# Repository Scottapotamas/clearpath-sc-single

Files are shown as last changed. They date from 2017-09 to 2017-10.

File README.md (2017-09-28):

# clearpath-sc-single

A cut down board with similar electronics to the Clearpath SC4-Hub, but designed for single motor use.

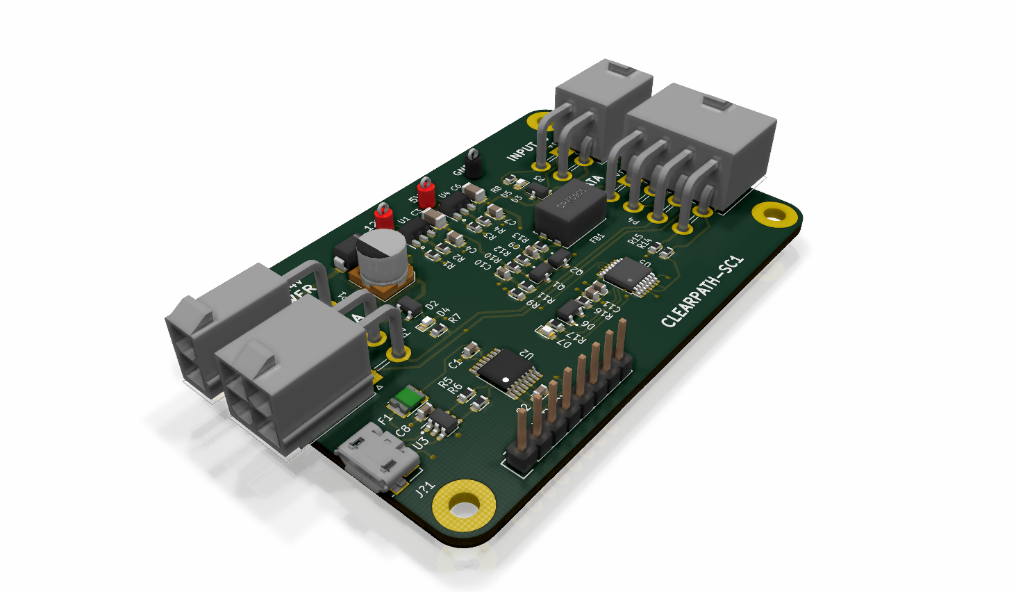
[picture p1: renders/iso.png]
Iso Render SC Single Render Iso View


## Overview

The Clearpath line of CNC servo motors from Teknic are great for robotics due to tight integration of controller and motor.

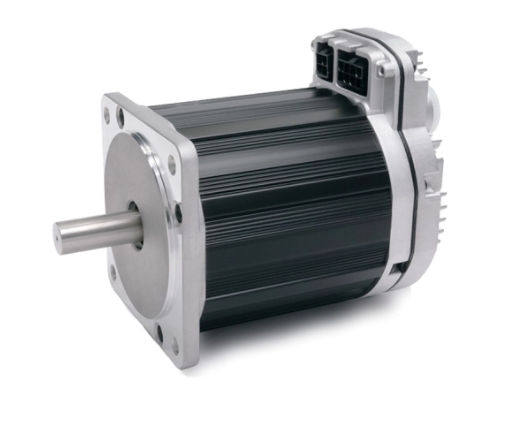
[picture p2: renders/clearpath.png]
Clearpath Motor

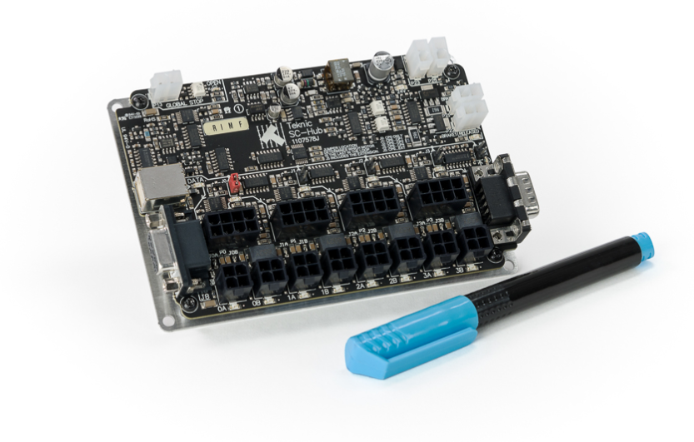
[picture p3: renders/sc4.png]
SC4 Hub Teknic's SC4 Hub


The SC series are software controllable, but rely on the use of a communications hub for level shifting and e-stop etc. This hub is designed to handle 4 motors and daisy chaining, and offers outputs to control brake solenoids and e-stop switches.

My application is space constrained and has no brake, so this single channel board offers the same main functionality (but we lose e-stop and brake outputs, and less defensive filtering on power input) in a reduced form factor. The serial input and USB functionality is maintained, and all OEM level hardening/filtering on communication lines on the SC4 is maintained. 

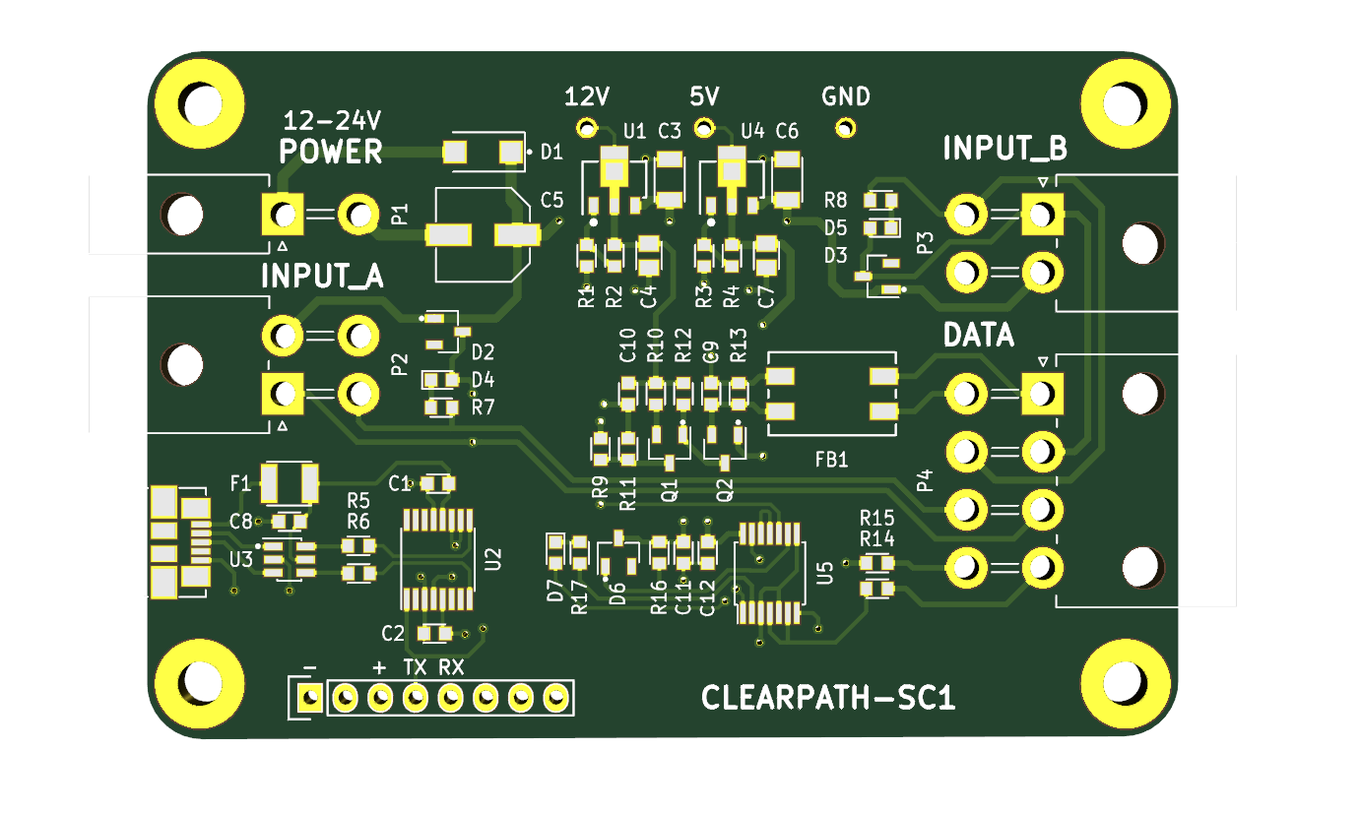
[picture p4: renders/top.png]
Top Render SC Single Render Top View


12-24V input power to provide signal level power. USB to serial is powered from the USB host. Header supports other TTL level serial devices if desired.

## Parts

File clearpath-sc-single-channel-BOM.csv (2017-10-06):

Title: | Single Channel Clearpath SC IO Board
Rev: | 1.0
Source: | /home/scott/projects/clearpath-sc-single/clearpath-sc-single-channel/clearpath-sc-single-channel.sch
Date: | Fri 06 Oct 2017 14:04:01 ACDT
Component Count: | 54
Ref | Qty | Value | Description | Manf | Manf# | Installed | Footprint
C1, C2, C8, C10, C11, C12 | 6 | 100NF_X7R_1608M | CAP, MLCC, X7R, 100NF, 50V, 0603 | KEMET | C0603C104K5RACAUTO |  | CAPC1608X90N
C3, C6 | 2 | 1UF_X7R_3216M | CAP, MLCC, X7R, 1UF, 100V, 1206, 3216M | TDK | C3216X7R2A105K160AA |  | CAPC3216X135N
C4, C7 | 2 | 1UF_X7R_2012M | CAP, MLCC, X7R, 1UF, 16V, 0805, 2012M | MURATA | GRM21BR71C105KA01L |  | CAPC2012X110N
C5 | 1 | 100UF_ELEC_35V_660X580M | CAP, ALU ELEC, 100UF, 35V, SMD | PANASONIC | EEEFT1V101AP |  | CAPAE660X580DD180L260N
C9 | 1 | 33NF_X7R_1608M | CAP, MLCC, X7R, 33NF, 50V, 0603 | KEMET | C0603C333K5RACAUTO |  | CAPC1608X90N
D1 | 1 | 1000V_1A_SODFL5125 | DIODE, 1000V, 1A, DO-214AC | MULTICOMP | S1M |  | SODFL5125X250N
D2, D3, D6 | 3 | BAS21_SOT23 | DIODE, 250V, 1.25Vfd, 2A surge, 50ns, SOT23 | ON SEMICONDUCTOR | BAS21 |  | SOT95P240X110-3L16N
D4, D5, D7 | 3 | LED_GREEN_1608M | DIALIGHT ChipLED Green, 0603, 1608M | DIALIGHT | 5988070107F |  | LEDC1608X80L40N
F1 | 1 | 500mA_1210L_PTC | FUSE, RESETTABLE, PTC, 13.2VDC, 500mA, SMD, 1210L050 | LittelFuse | 1210L050YR |  | FUSC3225X85L50N
FB1 | 1 | CHOKE_6500uH_300mA_0.3-2MHz | LINE FILTER, 6500uH, 80V, 300mA, 0.3-2Mhz, SMD | BOURNS | SRF0905-652Y |  | SRF0905
J?1 | 1 | USB_MICRO_B_SMD_2 | MICRO USB B RIGHT ANGLE FEMALE MOLEX | Molex | 47346-0001 |  | MOLEX_47346-0001
P1 | 1 | MOLEX_MICROFIT_JR_RH_2x1_WAY | CONNECTOR, SOCKET, 2POS, 1ROW, MICRO-FIT JR, 5569 series, 4.2MM pitch, PTH | MOLEX | 50-36-2457 |  | Molex_MiniFit-JR-5569-02A2_2x01x4.20mm_Angled
P2, P3 | 2 | MOLEX_MICROFIT_JR_RH_2x2_WAY | CONNECTOR, SOCKET, 4POS, 2ROW, MICRO-FIT JR, 5569 series, 4.2MM pitch, PTH | MOLEX | 26-01-3115 |  | Molex_MiniFit-JR-5569-04A2_2x02x4.20mm_Angled
P4 | 1 | MOLEX_MICROFIT_JR_RH_2x4_WAY | CONNECTOR, SOCKET, 8POS, 4ROW, MICRO-FIT JR, 5569 series, 4.2MM pitch, PTH | MOLEX | 172448-0008 |  | Molex_MiniFit-JR-5569-08A2_2x04x4.20mm_Angled
P5 | 1 | CONN_01X08 | Pin Header, 2.54mm, Vertical, PTH, 8 Way, 1 Row, 01x08 | WURTH | 61300811121 |  | 61300811121
Q1 | 1 | MMBT5401 | Transistor, PNP, -150V, 300MHz, 600mA, 250mW, SOT23 | ON SEMI | MMBT5401 |  | SOT95P240X110-3L16N
Q2 | 1 | MMBTA06 | Transistor, NPN, 80V, 100MHz, 500mA, 350mW, SOT-23 | ON SEMI | MMBTA06 |  | SOT95P240X110-3L16N
R1 | 1 | 2K2_1608M | RESISTOR, THICK FILM, 2.2K, 100mW, 1%, 0603, 1608M | VISHAY | CRCW06032K20FKEA |  | RESC1608X50N
R10 | 1 | 768R_1608M | RESISTOR, THICK FILM, 768R, 100mW, 1%, 0603, 1608M | PANASONIC | ERJ3EKF7680V |  | RESC1608X50N
R11 | 1 | 4K7_1608M | RESISTOR, THICK FILM, 100K, 125mW, 1%, 0603, 1608M | MULTICOMP | MC0063W060354K7 |  | RESC1608X50N
R12 | 1 | 93K1_1608M | RESISTOR, THICK FILM, 93.1K, 100mW, 1%, 0603, 1608M | VISHAY | CRCW060393K1FKEA |  | RESC1608X50N
R13 | 1 | 560R_1608M | RESISTOR, THICK FILM, 560R, 125mW, 1%, 0603, 1608M | MULTICOMP | MC0201L6F5600SE |  | RESC1608X50N
R14, R15 | 2 | 62R_1608M | RESISTOR, THICK FILM, 62R, 63mW, 0603, 1608M | MULTICOMP | MC00625W0402162R |  | RESC1608X50N
R16 | 1 | 470K_1608M | RESISTOR, THICK FILM, 470K, 100mW, 1%, 0603, 1608M | PANASONIC | ERJ3EKF4703V |  | RESC1608X50N
R17 | 1 | 390R_1608M | RESISTOR, THICK FILM, 390R, 63mW, 1%, 0603, 1608M | MULTICOMP | MC0063W06031390R |  | RESC1608X50N
R2, R4 | 2 | 240R_1608M | RESISTOR, THICK FILM, 240R, 100mW, 1%, 0603, 1608M | VISHAY DRALORIC | CRCW0603240RFKEA |  | RESC1608X50N
R3 | 1 | 750R_1608M | RESISTOR, THICK FILM, 750R, 100mW, 0603, 1608M | PANASONIC | ERJ3GEYJ751V |  | RESC1608X50N
R5, R6 | 2 | 22R_1608M | RESISTOR, THICK FILM, 22R, 125mW, 1%, 0603, 1608M | MULTICOMP | MC0063W060314R22 |  | RESC1608X50N
R7, R8 | 2 | 2K40_1608M | RESISTOR, THICK FILM, 2K4, 63mW, 1%, 0603, 1608M | MULTICOMP | MC0063W060312K4 |  | RESC1608X50N
R9 | 1 | 1K00_1608M | RESISTOR, THICK FILM, 1K, 125mW, 1%, 0603, 1608M | MULTICOMP | MCHP03W8F1001T5E |  | RESC1608X50N
TEST1, TEST2 | 2 | CLIP_HOOK_RED | PCB Probe Hook, RED, Through Hole | KEYSTONE | 5000 |  | KEYSTONE_5000
TEST3 | 1 | CLIP_HOOK_BLACK | PCB Probe Hook, BLACK, Through Hole | KEYSTONE | 5001 |  | KEYSTONE_5001
U1, U4 | 2 | LM317LCPK | ADJUSTABLE LINEAR REGULATOR, 1.2V TO 32V, SOT89-3 | TEXAS INSTRUMENTS | LM317LCPK |  | SOT89N
U2 | 1 | FT230XS-R | USB-UART/FIFO, USB2.0, FT230, SMD, TSSOP-16 | FTDI | FT230XS-R |  | SOP16P65_500X640X120L62X24N
U3 | 1 | USBLC6 | USBLC6-2 Low capacitance ESD Protection IC | ST | USBLC6-2SC6 |  | SOT95P280X145-6L50N
U5 | 1 | SN74HC14PWR | No description | TI | SN74HC14PWR |  | SOP14P65_500X640X120L62X24N
Tool: | Eeschema no-vcs-found
Script: | /home/scott/projects/ECAD/kicad-scripts/BOM/bom/BOM-GroupedByValue.py

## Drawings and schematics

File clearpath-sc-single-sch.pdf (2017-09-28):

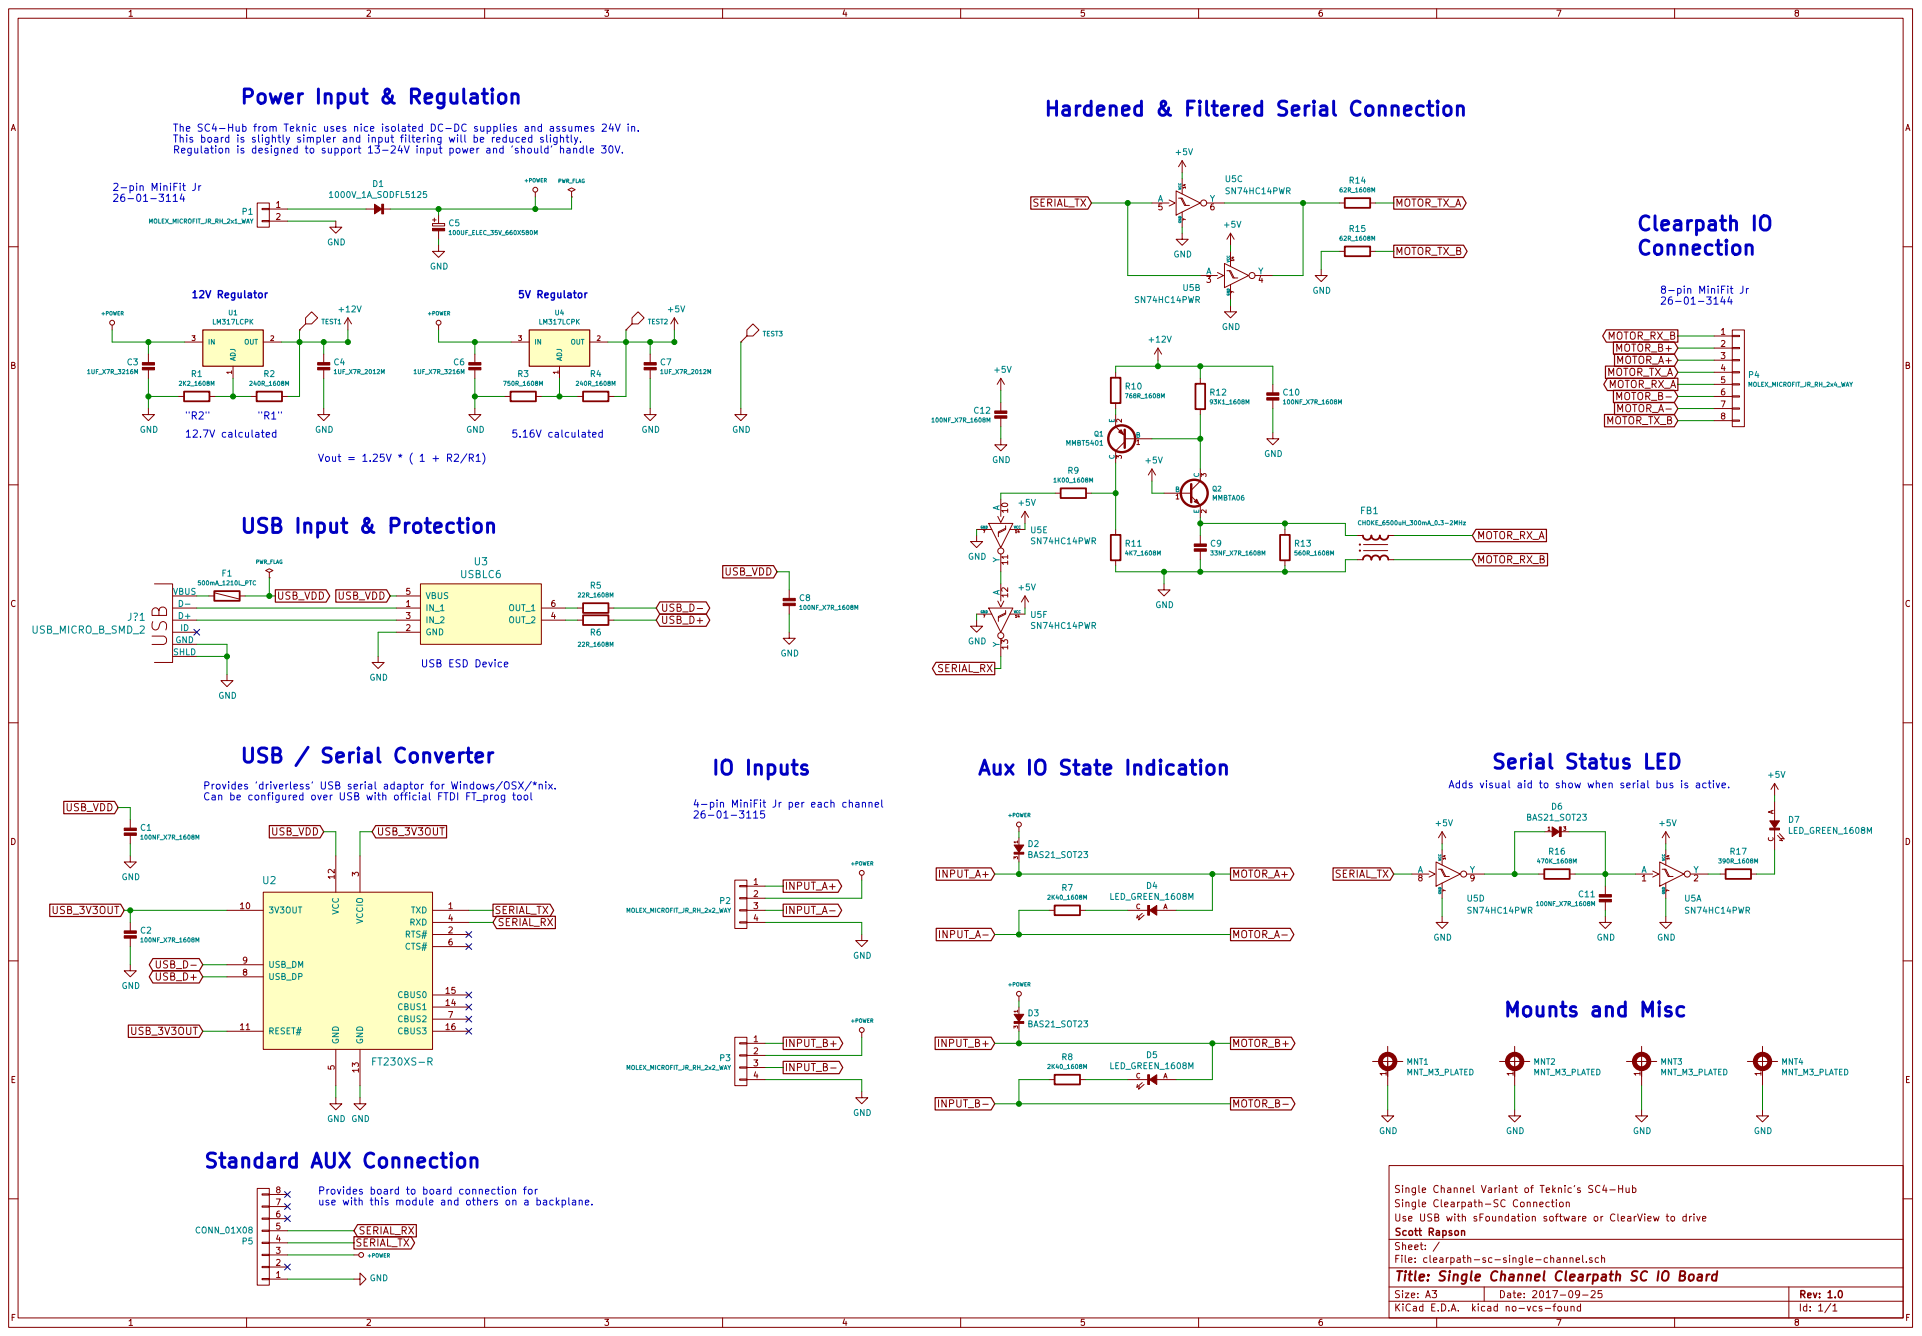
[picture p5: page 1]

4-pin MiniFit Jr per each channel 26-01-3115 Power Input & Regulation

Hardened & Filtered Serial Connection
8-pin MiniFit Jr 26-01-3144 Mounts and Misc

The SC4-Hub from Teknic uses nice isolated DC-DC supplies and assumes 24V in.
This board is slightly simpler and input filtering will be reduced slightly.

Single Channel Variant of Teknic's SC4-Hub USB VBUS D- D+

Aux IO State Indication

1 3 D3BAS21_SOT23 +POWER GND Adds visual aid to show when serial bus is active. USB_D-

Provides 'driverless' USB serial adaptor for Windows/OSX/*nix.
Can be configured over USB with official FTDI FT_prog tool

1 MNT1 MNT_M3_PLATED 1 MNT2 MNT_M3_PLATED 1 MNT3 MNT_M3_PLATED 1 MNT4 MNT_M3_PLATED GND GND GND GND

Provides board to board connection for use with this module and others on a backplane.

File: clearpath-sc-single-channel.sch Sheet: / Scott Rapson Use USB with sFoundation software or ClearView to drive Single Clearpath-SC Connection

Id: 1/1 Title: Single Channel Clearpath SC IO Board

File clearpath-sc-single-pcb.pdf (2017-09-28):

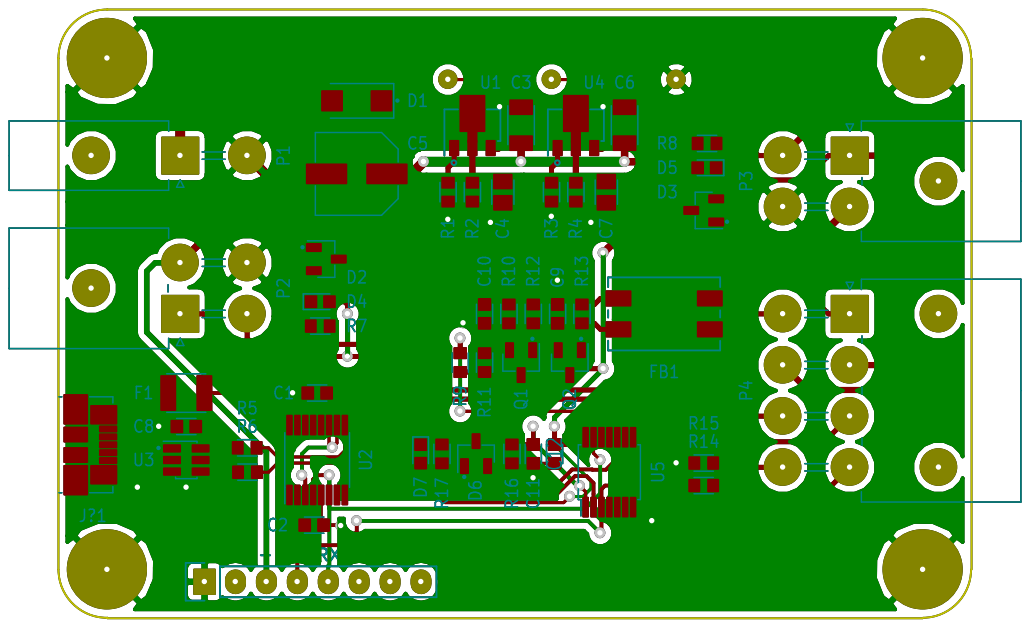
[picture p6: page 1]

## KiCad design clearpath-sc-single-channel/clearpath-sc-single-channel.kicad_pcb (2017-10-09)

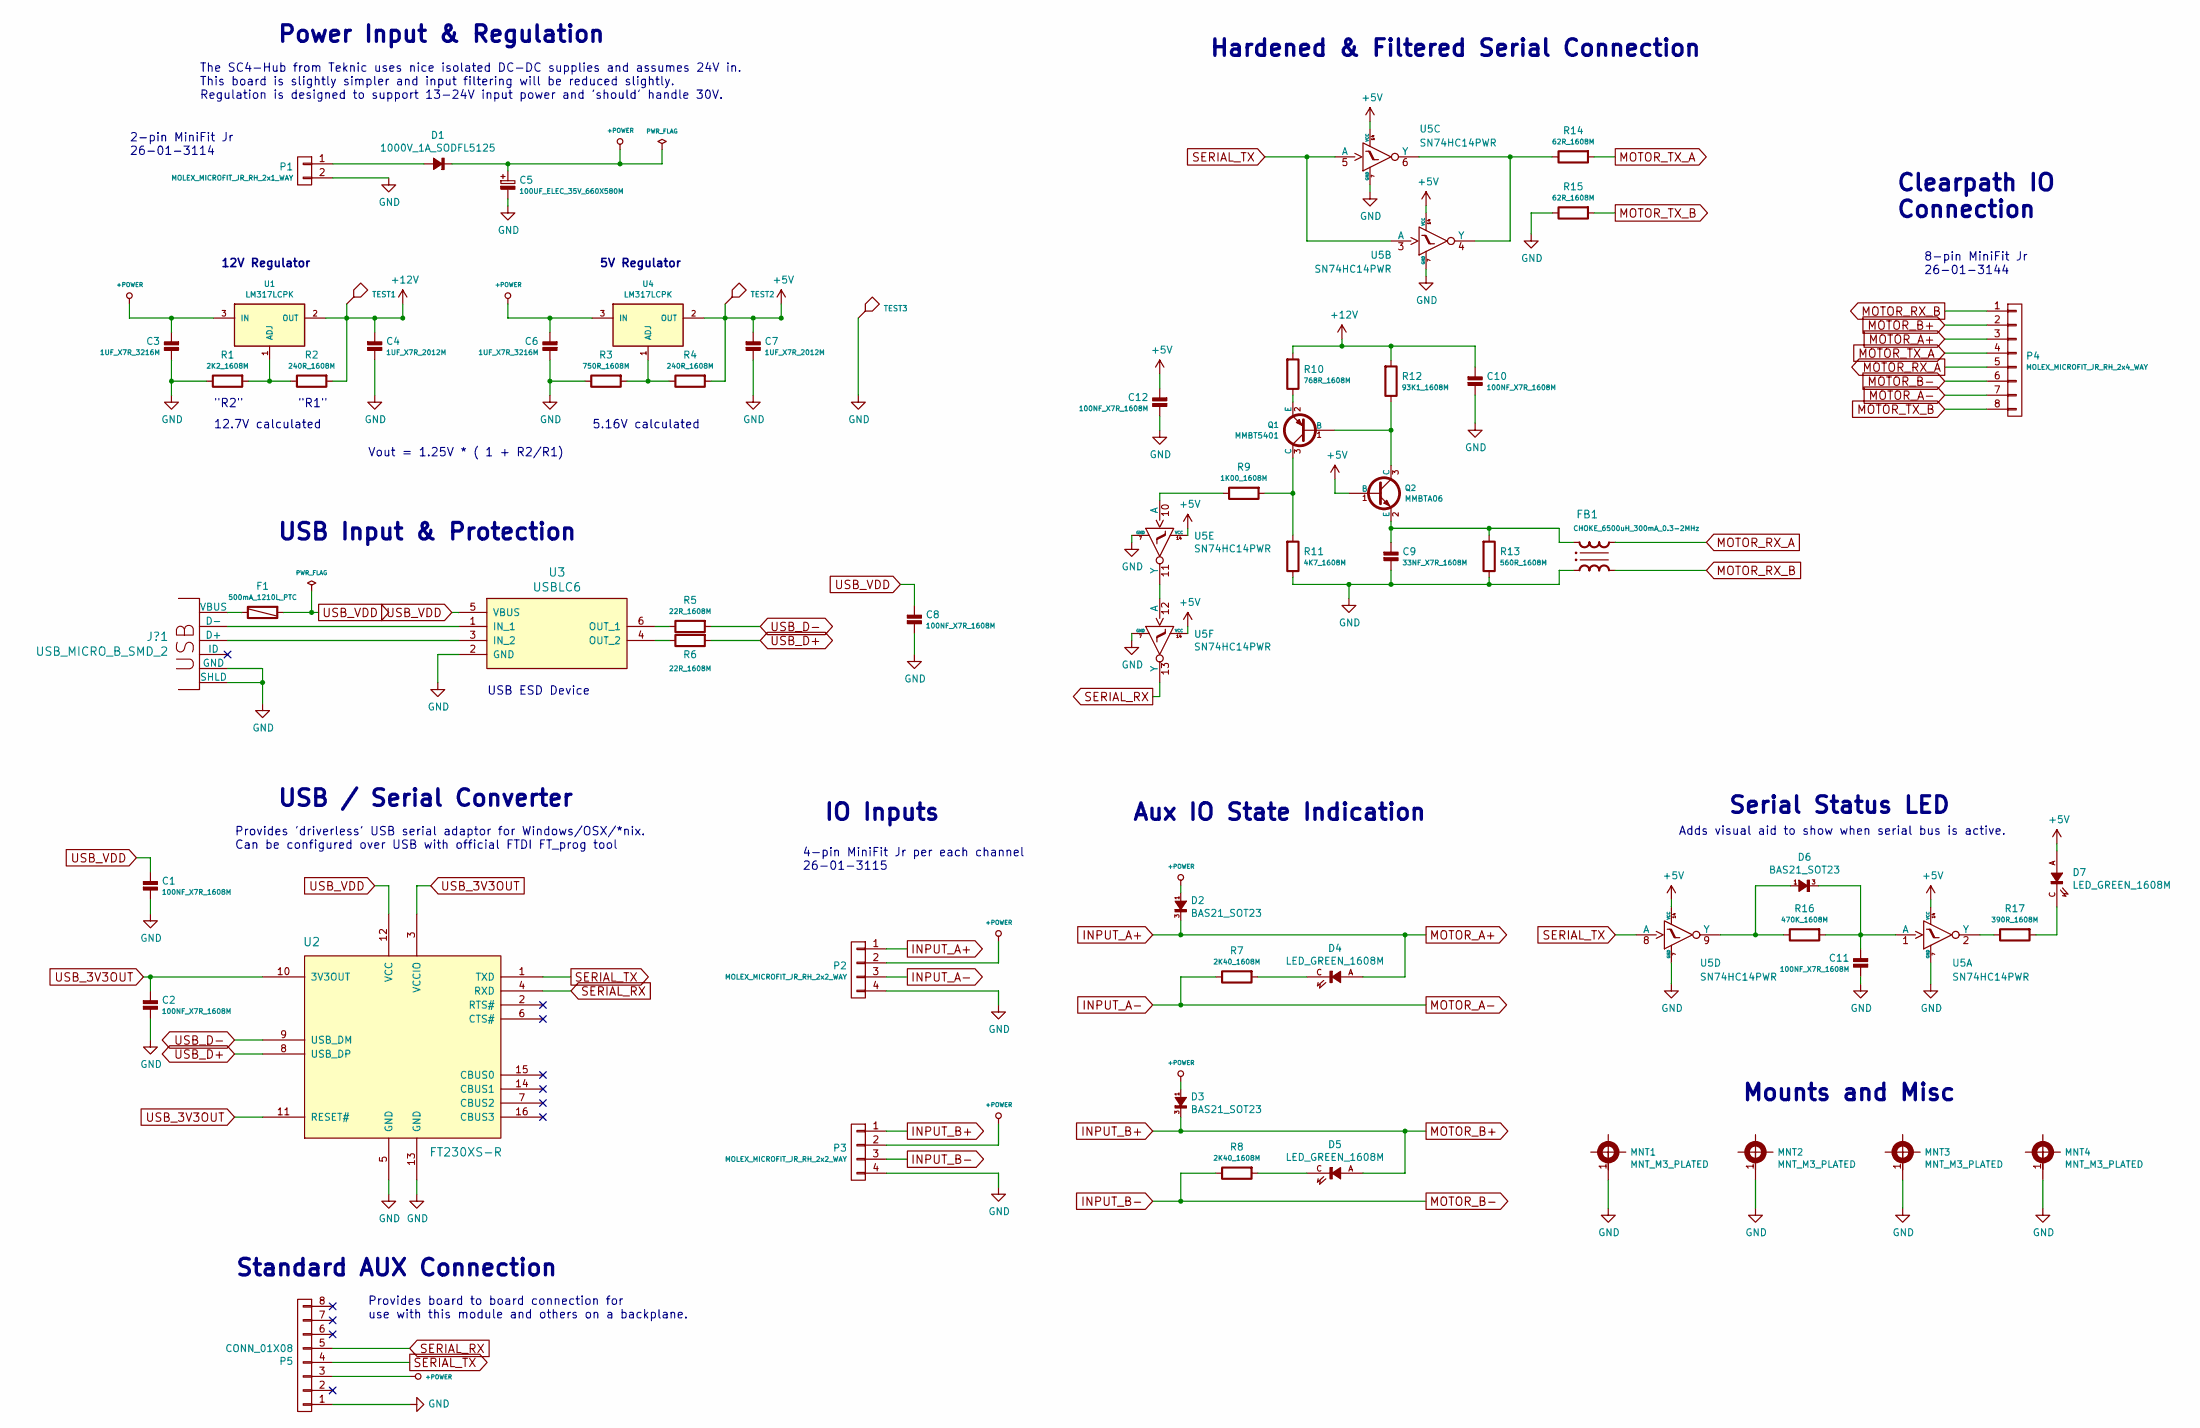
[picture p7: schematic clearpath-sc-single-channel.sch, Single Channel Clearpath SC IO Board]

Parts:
C1, C2, C8, C10, C11, C12: 100NF_X7R_1608M; CAPC1608X90N
C3, C6: 1UF_X7R_3216M; CAPC3216X135N
C4, C7: 1UF_X7R_2012M; CAPC2012X110N
C5: 100UF_ELEC_35V_660X580M; CAPAE660X580DD180L260N
C9: 33NF_X7R_1608M; CAPC1608X90N
D1: 1000V_1A_SODFL5125; SODFL5125X250N
D2, D3, D6: BAS21_SOT23; SOT95P240X110-3L16N
D4, D5, D7: LED_GREEN_1608M; LEDC1608X80L40N
F1: 500mA_1210L_PTC; FUSC3225X85L50N
FB1: CHOKE_6500uH_300mA_0.3-2MHz; SRF0905
J?1: USB_MICRO_B_SMD_2; MOLEX_47346-0001
MNT1, MNT2, MNT3, MNT4: MNT_M3_PLATED; MTGP650H330
P1: MOLEX_MICROFIT_JR_RH_2x1_WAY; Molex_MiniFit-JR-5569-02A2_2x01x4.20mm_Angled
P2, P3: MOLEX_MICROFIT_JR_RH_2x2_WAY; Molex_MiniFit-JR-5569-04A2_2x02x4.20mm_Angled
P4: MOLEX_MICROFIT_JR_RH_2x4_WAY; Molex_MiniFit-JR-5569-08A2_2x04x4.20mm_Angled
P5: CONN_01X08; 61300811121
Q1: MMBT5401; SOT95P240X110-3L16N
Q2: MMBTA06; SOT95P240X110-3L16N
R1: 2K2_1608M; RESC1608X50N
R2, R4: 240R_1608M; RESC1608X50N
R3: 750R_1608M; RESC1608X50N
R5, R6: 22R_1608M; RESC1608X50N
R7, R8: 2K40_1608M; RESC1608X50N
R9: 1K00_1608M; RESC1608X50N
R10: 768R_1608M; RESC1608X50N
R11: 4K7_1608M; RESC1608X50N
R12: 93K1_1608M; RESC1608X50N
R13: 560R_1608M; RESC1608X50N
R14, R15: 62R_1608M; RESC1608X50N
R16: 470K_1608M; RESC1608X50N
R17: 390R_1608M; RESC1608X50N
TEST1, TEST2: CLIP_HOOK_RED; KEYSTONE_5000
TEST3: CLIP_HOOK_BLACK; KEYSTONE_5001
U1, U4: LM317LCPK; SOT89N
U2: FT230XS-R; SOP16P65_500X640X120L62X24N
U3: USBLC6; SOT95P280X145-6L50N
U5: SN74HC14PWR; SOP14P65_500X640X120L62X24N

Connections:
+5V: C7.1, C12.1, D7.A, Q2.1 (B), R4.1, TEST2.1, U4.2 (OUT), U5.14 (VCC)
+12V: C4.1, C10.1, R2.1, R10.1, R12.1, TEST1.1, U1.2 (OUT)
+POWER: C3.1, C5.1, C6.1, D1.C, D2.1 (A), D3.1 (A), P2.2, P3.2, P5.3, U1.3 (IN), U4.3 (IN)
GND: C1.2, C2.2, C3.2, C4.2, C5.2, C6.2, C7.2, C8.2, C9.2, C10.2, C11.2, C12.2, FB1.1, J?1.5 (GND), J?1.SH (SHLD), MNT1.1, MNT2.1, MNT3.1, MNT4.1, P1.2, P2.4, P3.4, P5.1, R1.2, R3.2, R11.2, R13.2, R15.2, TEST3.1, U2.5 (GND), U2.13 (GND), U3.2 (GND), U5.7 (GND)
INPUT_A+: D2.3 (C), D4.A, P2.1, P4.3
INPUT_A-: P2.3, P4.7, R7.2
INPUT_B+: D3.3 (C), D5.A, P3.1, P4.2
INPUT_B-: P3.3, P4.6, R8.2
MOTOR_RX_A: FB1.3, P4.5
MOTOR_RX_B: FB1.4, P4.1
MOTOR_TX_A: P4.4, R14.1
MOTOR_TX_B: P4.8, R15.1
unnamed: C9.1, FB1.2, Q2.2 (E), R13.1
unnamed: C11.1, D6.3 (C), R16.1, U5.1 (A)
unnamed: D1.A, P1.1
unnamed: D4.C, R7.1
unnamed: D5.C, R8.1
unnamed: D6.1 (A), R16.2, U5.9 (Y)
unnamed: D7.C, R17.1
unnamed: F1.2, J?1.1 (VBUS)
unnamed: J?1.2 (D-), U3.1 (IN_1)
unnamed: J?1.3 (D+), U3.3 (IN_2)
unnamed: Q1.1 (B), Q2.3 (C), R12.2
unnamed: Q1.2 (E), R10.2
unnamed: Q1.3 (C), R9.1, R11.1
unnamed: R1.1, R2.2, U1.1 (ADJ)
unnamed: R3.1, R4.2, U4.1 (ADJ)
unnamed: R5.2, U3.6 (OUT_1)
unnamed: R6.2, U3.4 (OUT_2)
unnamed: R9.2, U5.10 (A)
unnamed: R14.2, U5.4 (Y), U5.6 (Y)
unnamed: R17.2, U5.2 (Y)
unnamed: U5.11 (Y), U5.12 (A)
SERIAL_RX: P5.5, U2.4 (RXD), U5.13 (Y)
SERIAL_TX: P5.4, U2.1 (TXD), U5.3 (A), U5.5 (A), U5.8 (A)
USB_3V3OUT: C2.1, U2.3 (VCCIO), U2.10 (3V3OUT), U2.11 (RESET#)
USB_D+: R6.1, U2.8 (USB_DP)
USB_D-: R5.1, U2.9 (USB_DM)
USB_VDD: C1.1, C8.1, F1.1, U2.12 (VCC), U3.5 (VBUS)

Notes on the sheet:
USB Input & Protection
Clearpath IO Connection
IO Inputs
4-pin MiniFit Jr per each channel 26-01-3115
Power Input & Regulation
2-pin MiniFit Jr 26-01-3114
8-pin MiniFit Jr 26-01-3144
Mounts and Misc
Hardened & Filtered Serial Connection
Aux IO State Indication
Serial Status LED
USB / Serial Converter
Adds visual aid to show when serial bus is active.
USB ESD Device
Provides 'driverless' USB serial adaptor for Windows/OSX/*nix. Can be configured over USB with official FTDI FT_prog tool
The SC4-Hub from Teknic uses nice isolated DC-DC supplies and assumes 24V in. This board is slightly simpler and input filtering will be reduced slightly. Regulation is designed to support 13-24V input power and 'should' handle 30V.
12V Regulator
5V Regulator
"R1"
"R2"
Vout = 1.25V * ( 1 + R2/R1)
12.7V calculated
5.16V calculated
Standard AUX Connection
Provides board to board connection for use with this module and others on a backplane.

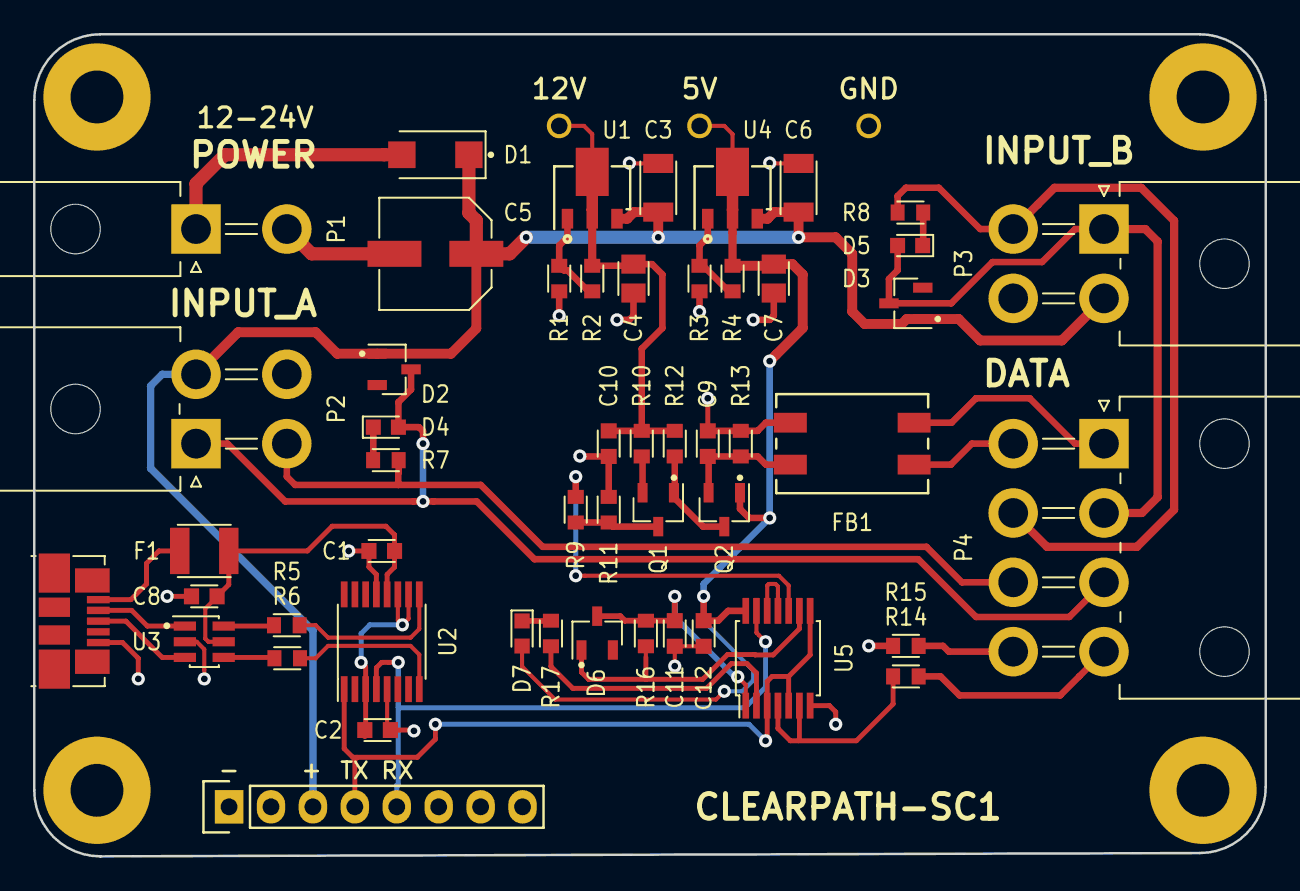
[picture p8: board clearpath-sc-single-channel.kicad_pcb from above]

Board: 2 copper layers, 74.6 x 49.8 mm, 58 parts (0 on the bottom side), 39 nets.

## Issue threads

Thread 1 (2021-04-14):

Schmitt-Trigger SN74HC14PWR wrong Pinout

tobawo, 2021-04-14:
Thanks @Scottapotamas for sharing the single version of the clearpath hub!

I wanted to report an error so that others do not run into the same problem:
- The pins of the right side (Pin 8-14) of the Schmitt-Trigger IC are swapped in your schematic symbol and therefore in the layout as well (A <--> Y).

- R12 should probably ~90 Ohm instead of ~90 **k**Ohm?

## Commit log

2017-09-24 Initial pass at schematic
    Most connectors and filter/protection circuitry sch captured.
    Needs USB-TTL adaptor and power stuff still.
    [clearpath-sc-single-channel.kicad_pcb, clearpath-sc-single-channel.sch]
2017-09-25 Added serial and regulator ICs
    FT230 series USB TTL IC added, 12 and 5V linear regs added.
    Reorganised some content and fixed label directions.
    [clearpath-sc-single-channel.sch]
2017-09-25 Regulator and input circuits finished.
    Added pdf of current sch and updated readme.
    [clearpath-sc-single-channel.sch]
2017-09-27 Annotated and DRC checks
    Fixed some DRC warnings.
    [clearpath-sc-single-channel.sch]
2017-09-27 Full footprint association, netlist generation
    DRC passes with no errors, ready for layout.
    [clearpath-sc-single-channel.sch]
2017-09-27 Started routing
    Placement complete, most signal routing done or nearly finished.
    [_saved_clearpath-sc-single-channel.sch, clearpath-sc-single-channel.kicad_pcb]
2017-09-27 Reworked hex inverter and finished routing
    Increased trace thickness, all drc errors removed, improved hex schmitt wiring by shuffling unit allocation in schematic.
    [_saved_clearpath-sc-single-channel.sch, clearpath-sc-single-channel.kicad_pcb, clearpath-sc-single-channel.sch]
2017-09-27 Cosmetic improvements
    Added silkscreen text and voltage test points
    [clearpath-sc-single-channel.kicad_pcb, clearpath-sc-single-channel.sch]
2017-09-28 Added aux connector, silkscreen labels and some final touches.
    Ready for final check (pinout against SC4) and fab outputs
    [clearpath-sc-single-channel.sch]
2017-09-28 Resolved missing 3d models on connector and line filter footprints. Exported PCB pdf
    [clearpath-sc-single-channel.kicad_pcb]
2017-09-29 Shrunk board outline slightly to improve tolerances
    Useful if mated to a backplane, would allow two within a 100mm long edge area.
    [clearpath-sc-single-channel.kicad_pcb]
2017-10-06 Added BoM
    [clearpath-sc-single-channel-BOM.csv]
2017-10-06 Added gerbers
    [clearpath-sc-single-channel-B.Cu.gbr, clearpath-sc-single-channel-B.Fab.gbr, clearpath-sc-single-channel-B.Mask.gbr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]
2017-10-09 Fixed gap in outline layer, exported gerbers
    Fixes issue where copper layers don't export properly.
    [clearpath-sc-single-channel-B.Cu.gbr, clearpath-sc-single-channel-B.Fab.gbr, clearpath-sc-single-channel-B.Mask.gbr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]
